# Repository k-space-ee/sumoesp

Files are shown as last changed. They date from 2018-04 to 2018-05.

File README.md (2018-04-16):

# SumoESP

SumoESP is a [ESP32](https://espressif.com/en/products/hardware/esp32/overview)
based sumorobot similar to [SumoCHIP](https://github.com/eik-robo/sumochip).

Why yet another sumorobot design?

* SumoCHIP has it's issues listed under [known issues](https://github.com/eik-robo/sumochip#known-issues) section
* ESP32 has wireless interface and supports WebSockets which means we can keep same level of functionality
* ESP32 has hardware ADC-s which can be used with traditional IR distance
  sensors such as Sharp [Sharp GP2Y0A21YK0F](https://www.pololu.com/product/136)
* ESP32 has hardware PWM-s which means no more jerky behaviour with cheap servos
* ESP32 has just enough juice to run Micropython, so we don't have to rewrite everything

## Getting Micropython running

Fetch Xtensa toolchain, Espressif IoT Development Framework and Micropython fork:

```bash
wget https://dl.espressif.com/dl/xtensa-esp32-elf-linux64-1.22.0-61-gab8375a-5.2.0.tar.gz
tar xvf xtensa-esp32-elf-linux64-1.22.0-61-gab8375a-5.2.0.tar.gz

git clone https://github.com/espressif/esp-idf
cd esp-idf
git submodule update --init
git checkout f73c6f875cc564fa6c9962be71eac4dbdc56aa63
cd ..

git clone https://github.com/vandys/micropython-esp32/
cd micropython-esp32
git checkout e94cde8a735926ace3f6efe79cbc2b9ee83a9ee3
git submodule update --init
make -C mpy-cross
cd esp32
ESPIDF=../../esp-idf/ PATH=../../xtensa-esp32-elf/bin/:$PATH make deploy
```

Open up serial via USB cable:

```python
import machine
motor_left = machine.PWM(machine.Pin(34), 50)
motor_right = machine.PWM(machine.Pin(13), 50)
motor_left.duty(40)
motor_left.duty(77)
motor_left.duty(135)
```

## Bill of materials

Preliminary bill of materials:

- ESP32 4USD
- LiPo cell 3 USD
- Wheels 3 USD each
- Servos 6 USD each
- Ultrasonic distance sensor 1.3 USD or Sharp infrared sensors
- LiPo charger and protection module 1.5 USD
- LITEON LTH-209-01 sensors for line following 0.30 EUR each

Total less than 30USD, excluding either 3D printed case or DIY metal frame.

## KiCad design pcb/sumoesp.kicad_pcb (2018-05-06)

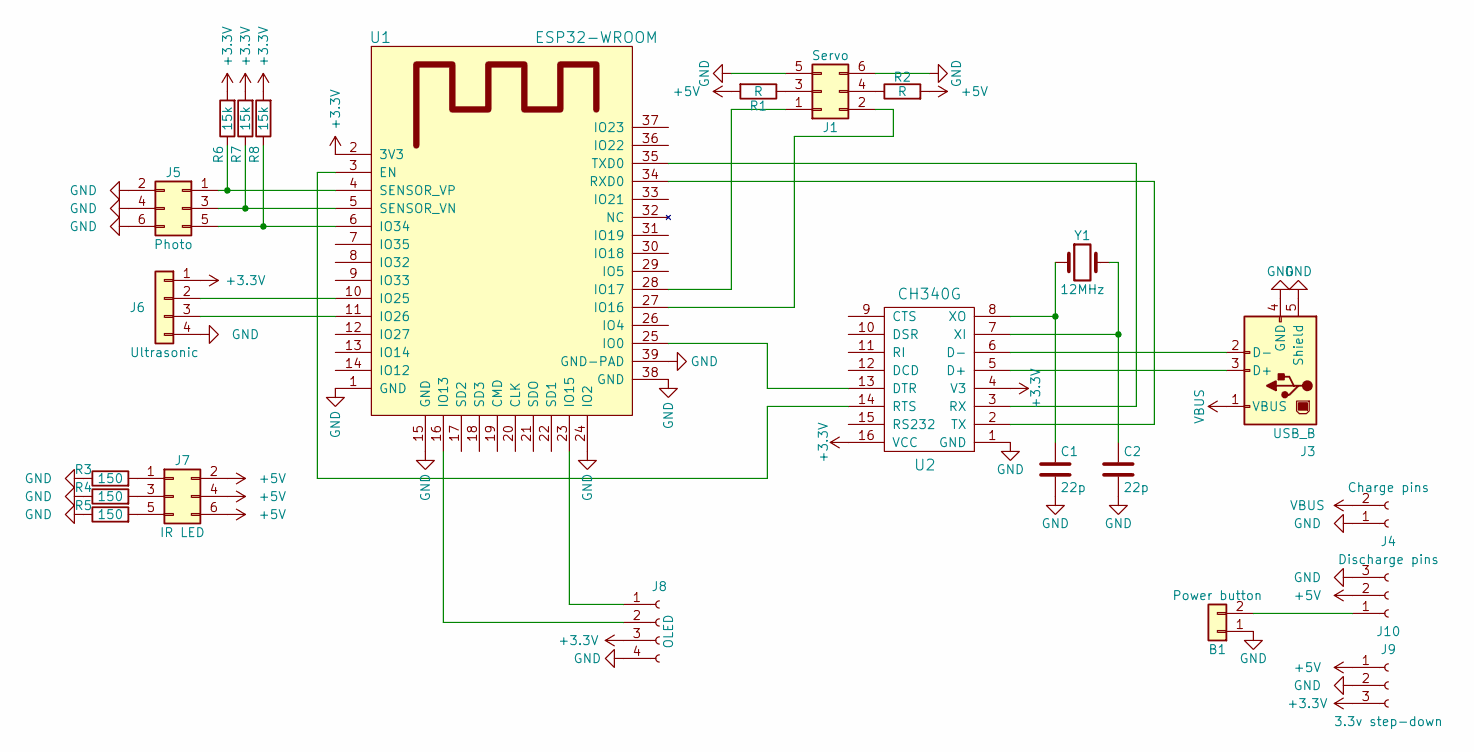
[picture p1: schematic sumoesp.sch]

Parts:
B1: Power button; SW_Tactile_SPST_Angled_PTS645Vx83-2LFS
C1, C2: 22p; C_Disc_D4.3mm_W1.9mm_P5.00mm
J1: Servo; Pin_Header_Angled_2x03_Pitch2.54mm
J3: USB_B
J4: Charge pins; Socket_Strip_Angled_1x02_Pitch2.54mm
J5: Photo; Pin_Header_Angled_2x03_Pitch2.54mm
J6: Ultrasonic; Pin_Header_Angled_1x04_Pitch2.54mm
J7: IR LED; Pin_Header_Angled_2x03_Pitch2.54mm
J8: OLED; Socket_Strip_Straight_1x04_Pitch2.54mm
J9: 3.3v step-down; Socket_Strip_Angled_1x03_Pitch2.54mm
J10: Discharge pins; Socket_Strip_Angled_1x03_Pitch2.54mm
R1, R2: R; R_Axial_DIN0207_L6.3mm_D2.5mm_P10.16mm_Horizontal
R3, R4, R5: 150; R_Axial_DIN0207_L6.3mm_D2.5mm_P7.62mm_Horizontal
R6, R7, R8: 15k; R_Axial_DIN0207_L6.3mm_D2.5mm_P7.62mm_Horizontal
U1: ESP32-WROOM
U2: CH340G; SOP-16_4.4x10.4mm_Pitch1.27mm
Y1: 12MHz; Crystal_HC49-U_Vertical

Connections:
+3V3: J6.1, J8.3, J9.3, R6.2, R7.2, R8.2, U1.2 (3V3), U2.4 (V3), U2.16 (VCC)
+5V: J7.2, J7.4, J7.6, J9.1, J10.2, R1.2, R2.2
GND: B1.1, C1.2, C2.2, J1.5, J1.6, J3.4 (GND), J3.5 (Shield), J4.1, J5.2, J5.4, J5.6, J6.4, J8.4, J9.2, J10.3, R3.1, R4.1, R5.1, U1.1 (GND), U1.15 (GND), U1.24 (IO2), U1.38 (GND), U1.39 (GND-PAD), U2.1 (GND)
unnamed: B1.2, J10.1
unnamed: C1.1, U2.8 (XO), Y1.1
unnamed: C2.1, U2.7 (XI), Y1.2
unnamed: J1.1, U1.28 (IO17)
unnamed: J1.2, U1.27 (IO16)
unnamed: J1.3, R1.1
unnamed: J1.4, R2.1
unnamed: J3.2 (D-), U2.6 (D-)
unnamed: J3.3 (D+), U2.5 (D+)
unnamed: J5.1, R6.1, U1.4 (SENSOR_VP)
unnamed: J5.3, R7.1, U1.5 (SENSOR_VN)
unnamed: J5.5, R8.1, U1.6 (IO34)
unnamed: J6.2, U1.10 (IO25)
unnamed: J6.3, U1.11 (IO26)
unnamed: J7.1, R3.2
unnamed: J7.3, R4.2
unnamed: J7.5, R5.2
unnamed: J8.1, U1.23 (IO15)
unnamed: J8.2, U1.16 (IO13)
unnamed: U1.3 (EN), U2.14 (RTS)
unnamed: U1.25 (IO0), U2.13 (DTR)
unnamed: U1.34 (RXD0), U2.2 (TX)
unnamed: U1.35 (TXD0), U2.3 (RX)
VBUS: J3.1 (VBUS), J4.2

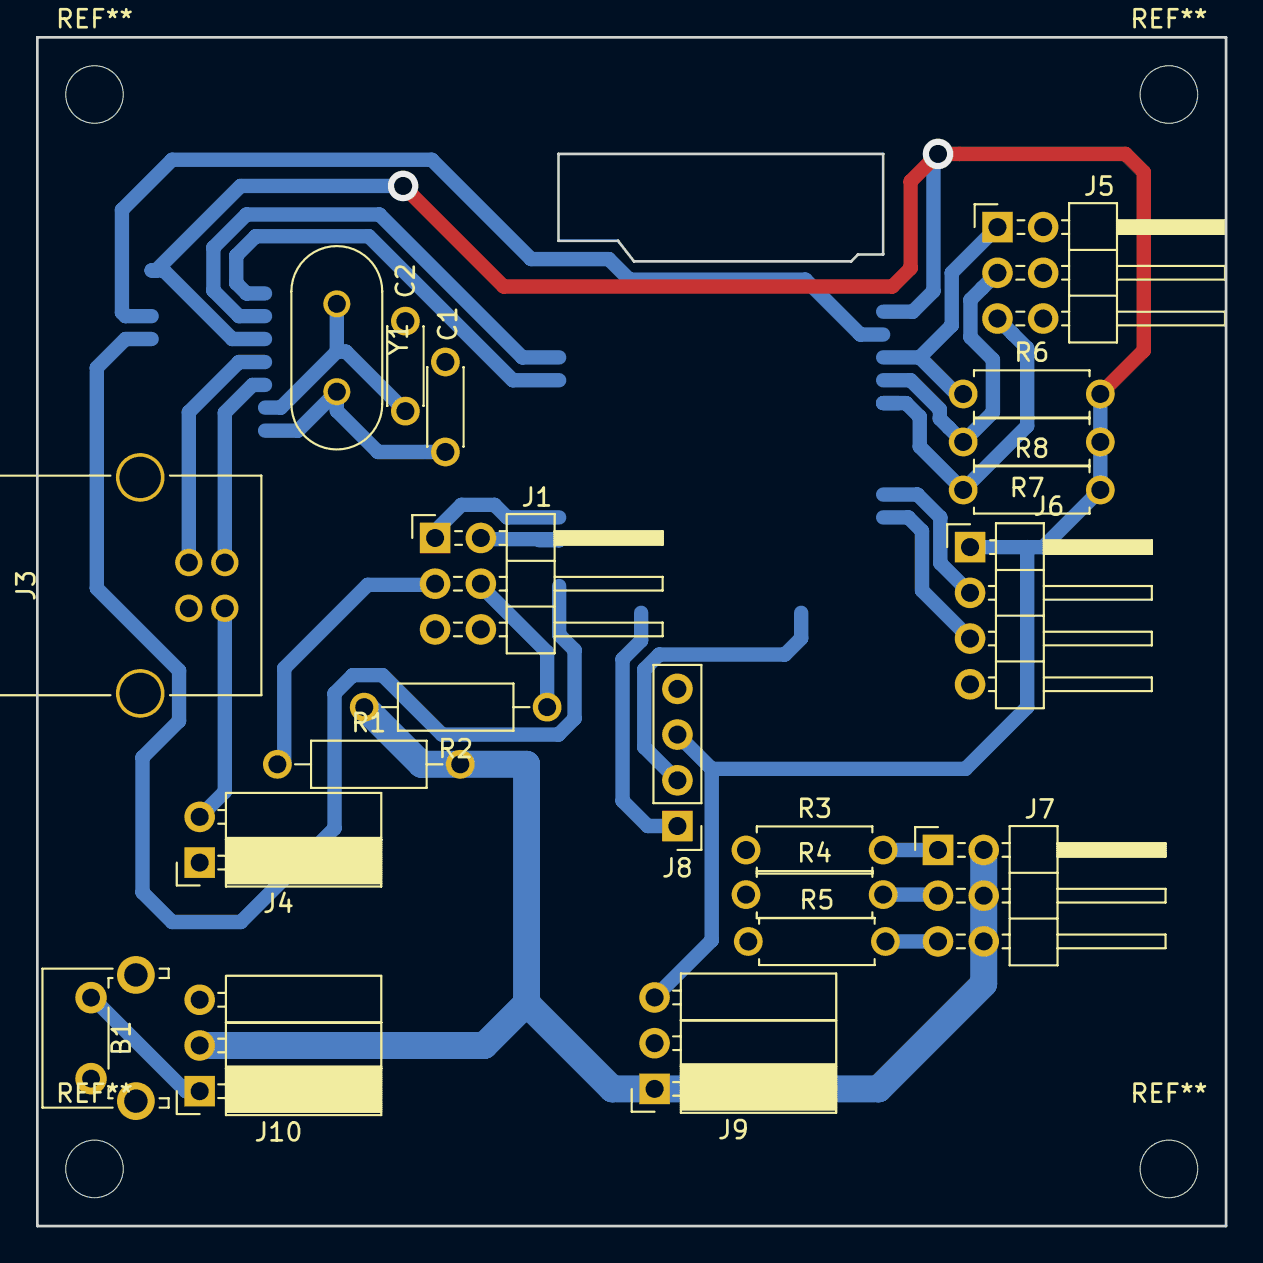
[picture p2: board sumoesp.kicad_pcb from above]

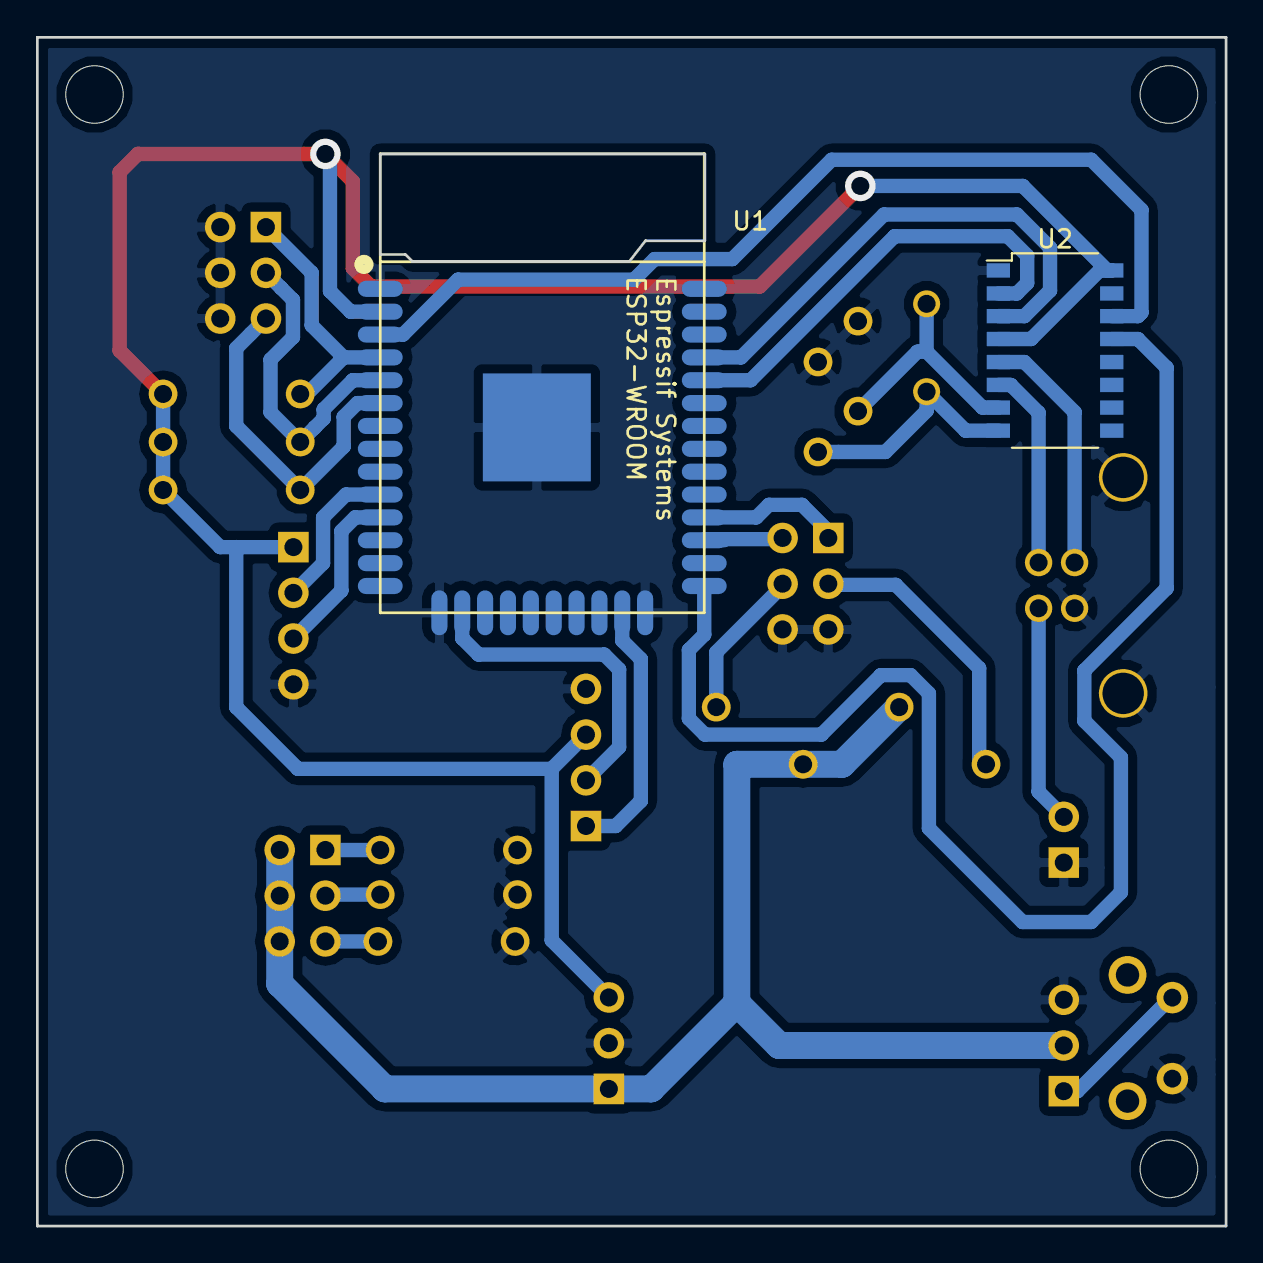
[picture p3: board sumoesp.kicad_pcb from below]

Board: 2 copper layers, 66.0 x 66.0 mm, 23 parts (2 on the bottom side), 27 nets.

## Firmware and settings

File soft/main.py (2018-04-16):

import _thread
import ubinascii
from utime import sleep_ms
from machine import Pin, PWM, Timer

conn = None
conn_highlight = None
name = "sumo-%s" % ubinascii.hexlify(wlan.config("mac")[-3:]).decode("ascii")

# remote nginx server
url = "ws://iot.koodur.com:80/p2p/" + name + "/browser/"
url_highlight = "ws://iot.koodur.com:80/p2p/" + name + "-highlight/browser/"

# local nginx server
#url = "ws://10.42.0.1:80/p2p/" + name + "/browser/"
#url_highlight = "ws://10.42.0.1:80/p2p/" + name + "-highlight/browser/"

scope = dict()
# send blocks IDs for highlighting
no_delay = False
highlight = True
ast = "move(STOP, '')"

def is_enemy(block_id):
    if block_id != "" and highlight:
        conn_highlight.send(block_id)
    return enemy_distance()

def is_line(dir, block_id):
    if block_id != "" and highlight:
        conn_highlight.send(block_id)
    if dir == LEFT:
        return line_left()
    elif dir == RIGHT:
        return line_right()
    return False

def move(dir, block_id):
    if block_id != "" and highlight:
        conn_highlight.send(block_id)
    if dir == STOP:
        motor_left(0)
        motor_right(0)
    elif dir == LEFT:
        motor_left(-100)
        motor_right(-100)
    elif dir == RIGHT:
        motor_left(100)
        motor_right(100)
    elif dir == FORWARD:
        motor_left(100)
        motor_right(-100)
    elif dir == BACKWARD:
        motor_left(-100)
        motor_right(100)

def move2(dir, block_id):
    if block_id != "" and highlight:
        conn_highlight.send(block_id)
    if dir == STOP:
        motor_left(0)
        motor_right(0)
    elif dir == RIGHT:
        motor_left(-100)
        motor_right(-100)
    elif dir == LEFT:
        motor_left(100)
        motor_right(100)
    elif dir == BACKWARD:
        motor_left(100)
        motor_right(-100)
    elif dir == FORWARD:
        motor_left(-100)
        motor_right(100)

def sleep_wrapper(delay, block_id):
    if block_id != "" and highlight:
        conn_highlight.send(block_id)
    for j in range(0, delay, 10):
        if ast == "move(STOP, '')":
            return # TODO: raise exception
        else:
            sleep_ms(10)

exported_functions = dict(
    STOP = STOP,
    LEFT = LEFT,
    RIGHT = RIGHT,
    FORWARD = FORWARD,
    BACKWARD = BACKWARD,
    move = move,
    is_line = is_line,
    is_enemy = is_enemy,
    sleep = sleep_wrapper,
    motor_left = motor_left,
    motor_right = motor_right
)

exported_functions2 = dict(
    STOP = STOP,
    LEFT = LEFT,
    RIGHT = RIGHT,
    FORWARD = FORWARD,
    BACKWARD = BACKWARD,
    move = move2,
    is_line = is_line,
    is_enemy = is_enemy,
    sleep = sleep_wrapper,
    motor_left = motor_left,
    motor_right = motor_right
)

def step():
    global scope

    shuffle = False
    while True:
        scope = dict(
            enemy = is_enemy(""),
            line_left = is_line(LEFT, ""),
            line_right = is_line(RIGHT, ""),
            battery_voltage = battery_voltage(),
        )
        if no_delay:
            if shuffle:
                current = exported_functions.copy()
            else:
                current = exported_functions2.copy()
            shuffle = not shuffle
        else:
            current = exported_functions.copy()
        current.update(scope)
        exec(ast, current)
        # leave time to process WebSocket commands
        sleep_ms(50)

def ws_handler():
    global ast
    global conn
    global scope
    global no_delay

    while True:
        try:
            fin, opcode, data = conn.read_frame()
        except: # urror
            print("Exception while reading from socket, attempting reconnect")
            conn = uwebsockets.connect(url)
            continue

        if data == b"forward":
            #print("Going forward")
            ast = "move(FORWARD, '')"
        elif data == b"backward":
            #print("Going backward")
            ast = "move(BACKWARD, '')"
        elif data == b"right":
            #print("Going right")
            ast = "move(RIGHT, '')"
        elif data == b"left":
            #print("Going left")
            ast = "move(LEFT, '')"
        elif data == b"kick":
            conn.send(repr(scope))
        elif data == b"ping":
            conn.send(repr(scope))
        elif data.startswith("start:"):
            print("Got code:")#, data[6:])
            if b"sleep" in data or b"if" in data or len(data.splitlines()) == 1:
                no_delay = False
            else:
                no_delay = True
            ast = compile(data[6:], "snippet", "exec")
        elif data == b"stop":
            ast = "move(STOP, '')"
            print("Got stop")
        elif b"Gone" in data:
            print("Server said 410 Gone, attempting to reconnect...")
            conn = uwebsockets.connect(url)
        else:
            print("unknown command:", data)

# wait for WiFi to get connected
while not wlan.isconnected():
    sleep_ms(100)

# connect to the websocket
print("Connecting to:", url)
conn = uwebsockets.connect(url)
print("Sending ping")
conn.send("{'ping': true}")
conn.send("{'ip': '" + wlan.ifconfig()[0] + "'}")
# connect to the block highlight websocket
conn_highlight = uwebsockets.connect(url_highlight)

# indicate that the WebSocket is connected
status_led(True)

print("Starting WebSocket and code loop")
# start the code processing thread
_thread.start_new_thread(step, ())
# start the Websocket processing thread
_thread.start_new_thread(ws_handler, ())

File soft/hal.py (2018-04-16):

from utime import sleep_us
from machine import Pin, PWM, ADC, time_pulse_us

WIFIS = dict({
"": ""})

# directions
STOP = 0
LEFT = 1
RIGHT = 2
FORWARD = 3
BACKWARD = 4

# Battery resistor ladder ratio
BATTERY_COEFF = 2.25

# Ultrasonic sensor calibration
ULTRASONIC_OFFSET = 800

# Servo timing
MOTOR_LEFT_TUNING = 33
MOTOR_RIGHT_TUNING = 33

# Motor PWM-s
pwm_left = PWM(Pin(16), freq=50, duty=0)
pwm_right = PWM(Pin(17), freq=50, duty=0)

# Sharp distance sensors
adc_enemy_left = ADC(Pin(36))
adc_enemy_right = ADC(Pin(37))

# Optek sensors
adc_line_left = ADC(Pin(32))
adc_line_middle = ADC(Pin(35))
adc_line_right = ADC(Pin(34))

# Ultrasonic distance sensor
trigger = Pin(25, Pin.OUT)
echo = Pin(26, Pin.IN)

# Battery gauge
adc_battery = ADC(Pin(33))

from time import sleep

# LED sweep
led_red = Pin(27, Pin.OUT, value=0)
sleep(0.2)
led_orange = Pin(14, Pin.OUT, value=0)
sleep(0.2)
led_green = Pin(12, Pin.OUT, value=0)
sleep(0.2)
led_blue = Pin(13, Pin.OUT, value=0)
sleep(0.2)
led_white = Pin(15, Pin.OUT, value=0)
sleep(0.2)
led_red.value(1)
sleep(0.2)
led_orange.value(1)
sleep(0.2)
led_green.value(1)
sleep(0.2)
led_blue.value(1)
sleep(0.2)
led_white.value(1)
sleep(0.2)

# Set reference voltage to 3.3V
adc_enemy_left.atten(ADC.ATTN_11DB)
adc_enemy_right.atten(ADC.ATTN_11DB)
adc_line_left.atten(ADC.ATTN_11DB)
adc_line_middle.atten(ADC.ATTN_11DB)
adc_line_right.atten(ADC.ATTN_11DB)
adc_battery.atten(ADC.ATTN_11DB)

# Calibrate line sensors
LINE_LEFT_THRESHOLD = adc_line_left.read()
LINE_MIDDLE_THRESHOLD = adc_line_middle.read()
LINE_RIGHT_THRESHOLD = adc_line_right.read()

def battery_voltage():
    return round(BATTERY_COEFF * (adc_battery.read() * 3.3 / 4096), 2)

enemy_score = 0
def enemy_distance():
    global enemy_score

    # send ping
    trigger.value(0)
    sleep_us(5)
    trigger.value(1)
    sleep_us(10)
    trigger.value(0)
    # wait for the pulse and calculate the distance
    enemy_distance = (time_pulse_us(echo, 1, 30000) / 2) / 29.1

    if enemy_distance < 60 and enemy_distance > 0:
        if enemy_score < 5:
            enemy_score += 1
    else:
        if enemy_score > 0:
            enemy_score -= 1

    # indicate enemy LED
    enemy_led.duty(255 if enemy_score > 2 else 0)

    return True if enemy_score > 2 else False

def line_left():
    return abs(adc_line_left.read() - LINE_LEFT_THRESHOLD) > 1000

def line_right():
    return abs(adc_line_right.read() - LINE_RIGHT_THRESHOLD) > 1000

def detach_servos():
    motor_left(0)
    motor_right(0)

prev_left_speed = 0
def motor_left(speed):
    global prev_left_speed
    if speed == prev_left_speed:
        return
    prev_left_speed = speed
    assert speed >= -100
    assert speed <= 100
    pwm_left.duty(int(33 + MOTOR_LEFT_TUNING + speed * 33 / 100)) # -100 ... 100 to 33 .. 102
    if speed == 0:
        pwm_left.duty(0)

prev_right_speed = 0
def motor_right(speed):
    global prev_right_speed
    if speed == prev_right_speed:
        return
    prev_left_speed = speed
    assert speed >= -100
    assert speed <= 100
    pwm_right.duty(int(33 + MOTOR_RIGHT_TUNING + speed * 33 / 100)) # -100 ... 100 to 33 .. 102
    if speed == 0:
        pwm_right.duty(0)

print("Battery voltage: %.2fV" % battery_voltage())
print("Line sensor thresholds:", LINE_LEFT_THRESHOLD, LINE_MIDDLE_THRESHOLD, LINE_RIGHT_THRESHOLD)

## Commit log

2018-04-16 add KiCad files
    [sumoesp.kicad_pcb, sumoesp.sch]
2018-05-06 update pcb layout
    [sumoesp.kicad_pcb, sumoesp.sch]
